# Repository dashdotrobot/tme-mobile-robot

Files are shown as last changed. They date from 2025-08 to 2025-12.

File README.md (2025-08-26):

# tme-mobile-robot
UW Tacoma Mechatronics mobile robotics platform for education

This repository contains 3D models, a parts list, and example code to build a simple two-wheeled robot. The required components are relatively cheap and easily available. A 3D printer and laser cutter are required to manufacture some components.

The robot can be easily extended and customized to accomplish a wide variety of tasks. The base plate has an array of holes which match the diameter and spacing of standard LEGO and LEGO Technic parts.

The robot platform was developed for TME 441 Mechatronics, a required senior-level course in the Mechanical Engineering program at the University of Washington, Tacoma.

## Parts list

### Base kit parts
These components are part of the base kit that every team assembles.

| Part | Qty | Source/Link
| ---- | --- | --- |
| Base plate | 1 | Custom (laser cut)
| Arduino Mega 2560 | 1 | [Amazon](https://www.amazon.com/ELEGOO-Compatible-Arduino-Projects-Compliant/dp/B01H4ZLZLQ)
| Motor bracket | 1 | Custom (3D print)
| Caster bracket - front | 1 | Custom (3D print)
| Caster bracket - rear | 1 | Custom (3D print)
| IR sensor bracket | 1 | Custom (3D print or laser cut)
| Wheel | 2 | Custom (3D print)
| LEGO Tire 81.6 x 15 ([#2902](https://www.bricklink.com/v2/catalog/catalogitem.page?P=2902)) | 2 | Various suppliers
| Gear motor with encoder | 2 | [Amazon](https://www.amazon.com/Encoder-Metal-Gearmotor-Arduino-Printers/dp/B07GNFYGYQ)
| 7.2V Battery pack | 1 | [Amazon](https://amazon.com/dp/B07NWZ4T29)
| Half-sized bread board | 1 | [Adafruit](https://www.adafruit.com/product/64)
| Analog IR sensor | 3 | [SparkFun](https://www.sparkfun.com/sparkfun-line-sensor-breakout-qre1113-analog.html)
| L293D Motor driver | 1 | [Amazon](https://www.amazon.com/Bridgold-16-pin-Stepper-Drivers-Controllers/dp/B07NXTWJV9)
| Ultrasonic sensor HC-SR04 | 1 | [SparkFun](https://www.sparkfun.com/products/15569)
| Plastic ball caster 1/2" | 2 | [Pololu](https://www.pololu.com/product/952)

### Expansion parts
These components are available to each team for use in their custom solution.

| Part | Qty | Source/Link |
| ---- | --- | --- |
| 5V Stepper motor 28BYJ-48 | 2 | [Amazon](https://www.amazon.com/ELEGOO-28BYJ-48-ULN2003-Stepper-Arduino/dp/B01CP18J4A)
| 9g Hobby servo | 2 | [Amazon](https://www.amazon.com/Smraza-Helicopter-Airplane-Control-Arduino/dp/B07L2SF3R4)
| Piezo buzzer | 1 | [Amazon](https://www.amazon.com/BNYZWOT-Electronic-Magnetic-Continuous-Arduino/dp/B07VP6BTMV)

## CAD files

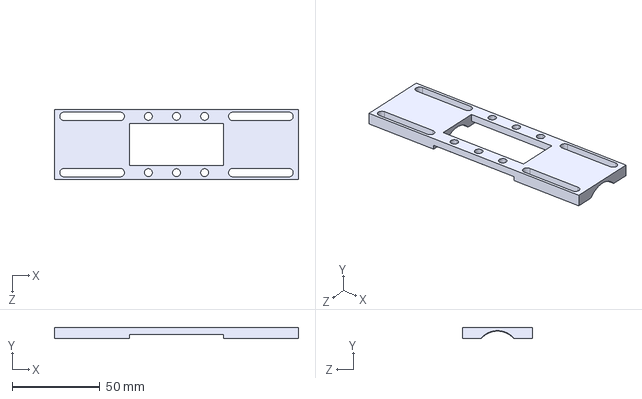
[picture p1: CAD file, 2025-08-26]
manufacturing files/motor_bracket_full.STEP
138.8 x 6.35 x 40.0 mm

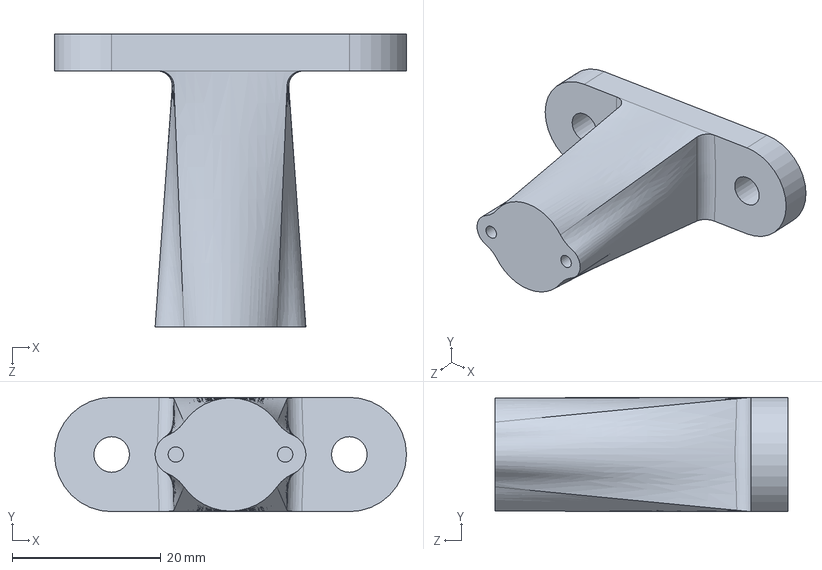
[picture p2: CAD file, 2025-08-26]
3d models/caster_bracket_rear.SLDPRT
47.4 x 15.4 x 39.5 mm

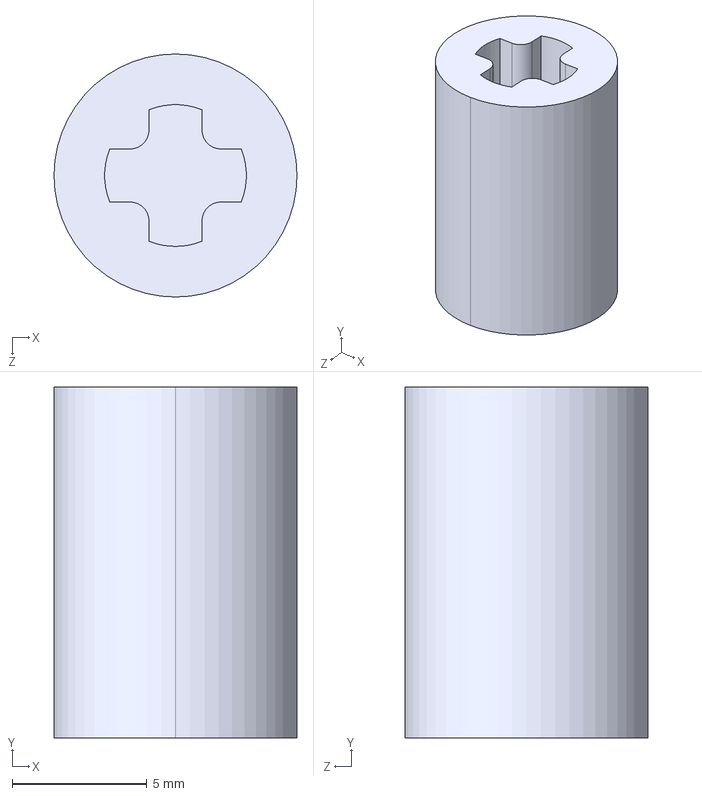
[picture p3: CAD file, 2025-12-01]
manufacturing files/stepper_motor_coupler.STEP
9.00 x 13.0 x 9.00 mm

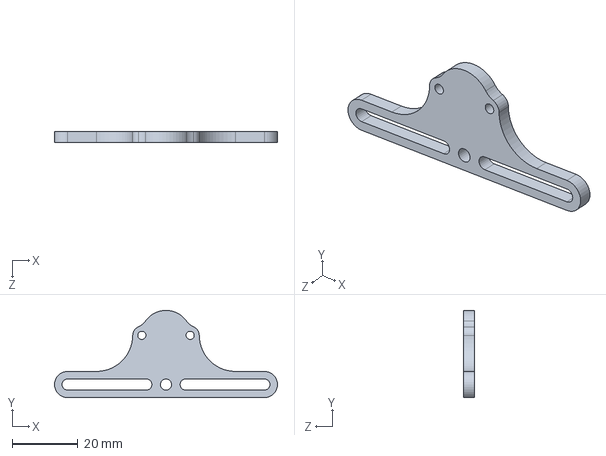
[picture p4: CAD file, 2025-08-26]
3d models/IR_sensor_bracket.SLDPRT
68.0 x 26.6 x 3.50 mm

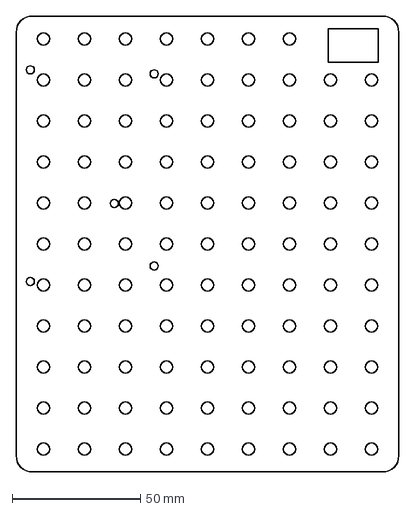
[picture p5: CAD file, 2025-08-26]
manufacturing files/base.DXF
149.2 x 177.8 mm

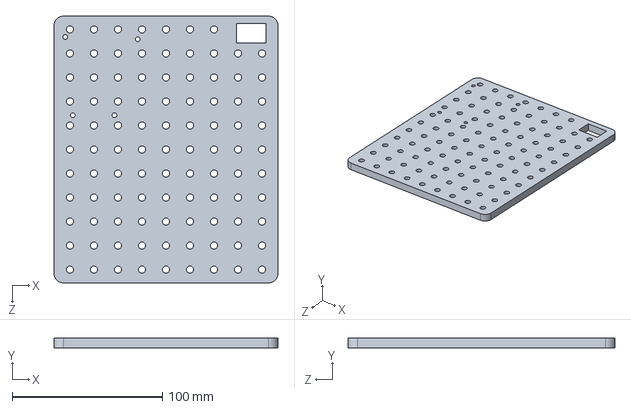
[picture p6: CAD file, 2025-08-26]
3d models/base.SLDPRT
149.2 x 6.35 x 177.8 mm

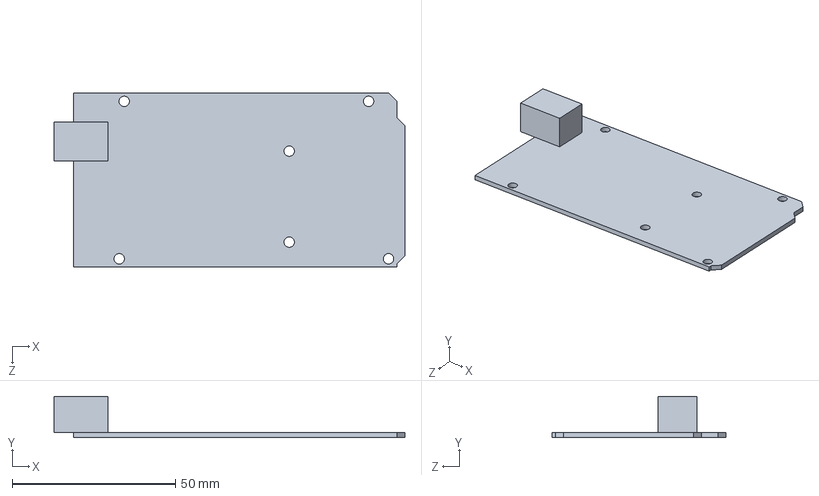
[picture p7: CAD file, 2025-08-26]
3d models/arduino_mega2560.SLDPRT
107.6 x 12.6 x 53.3 mm

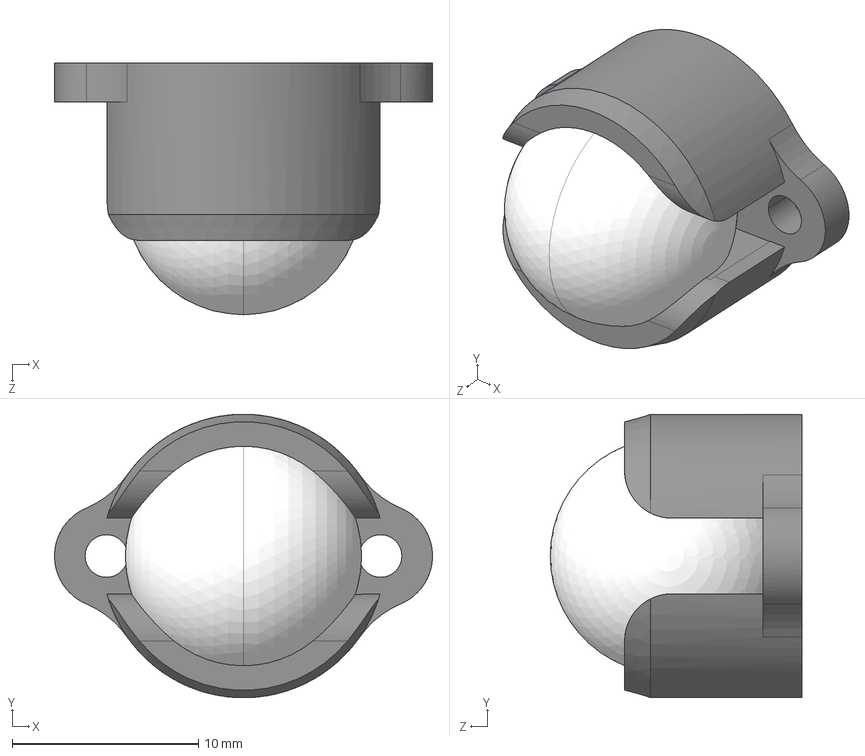
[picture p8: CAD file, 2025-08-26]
3d models/pololu-ball-caster-with-0-500in-ball.step
20.3 x 15.2 x 13.5 mm

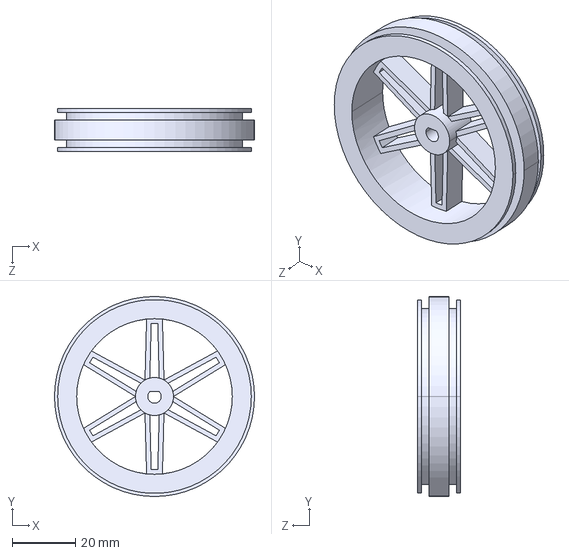
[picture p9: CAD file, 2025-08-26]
manufacturing files/wheel.STEP
63.1 x 63.1 x 13.5 mm

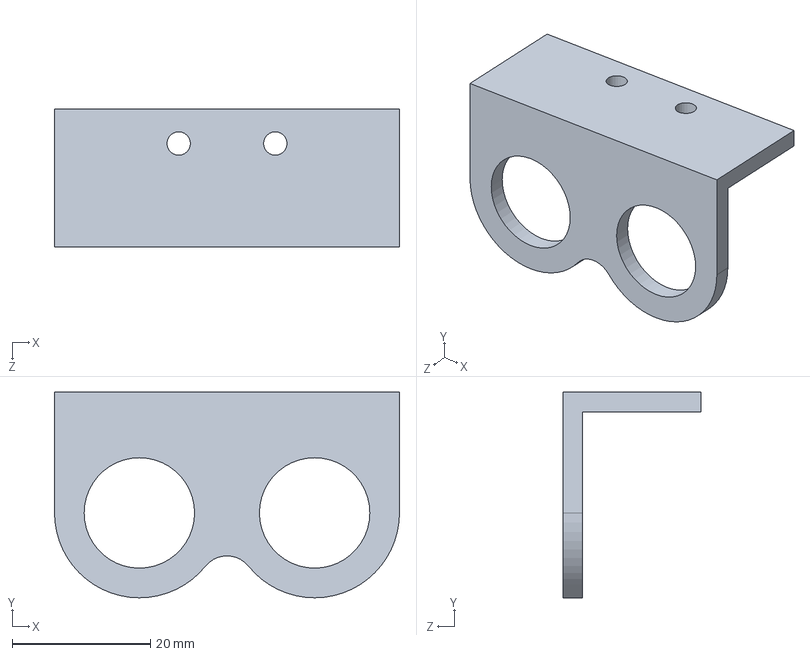
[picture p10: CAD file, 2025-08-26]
3d models/US_sensor_bracket.SLDPRT
50.0 x 29.8 x 20.0 mm

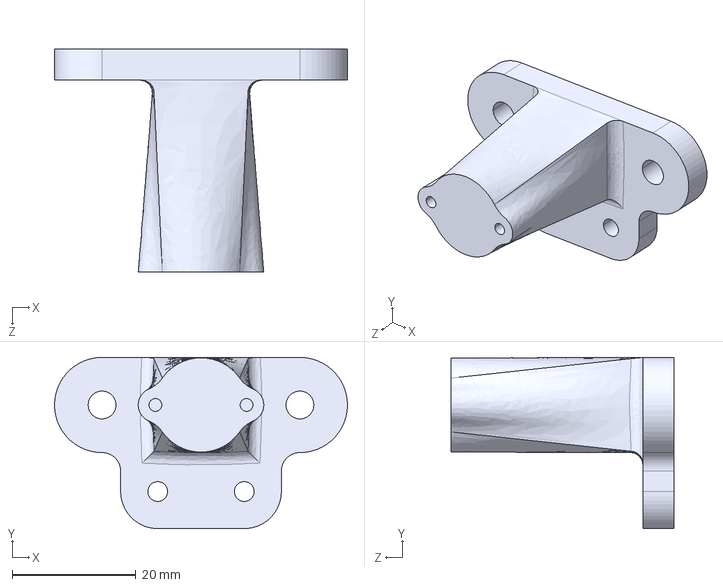
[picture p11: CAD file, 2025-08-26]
manufacturing files/caster_bracket_front.STEP
47.4 x 27.7 x 36.0 mm

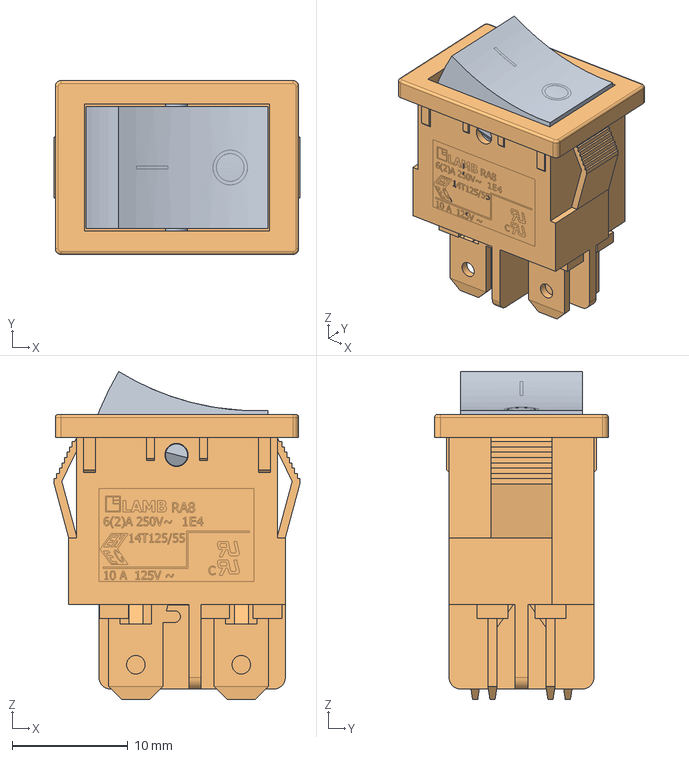
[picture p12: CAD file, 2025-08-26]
3d models/RA8123xxx1.stp
21.2 x 15.0 x 28.3 mm

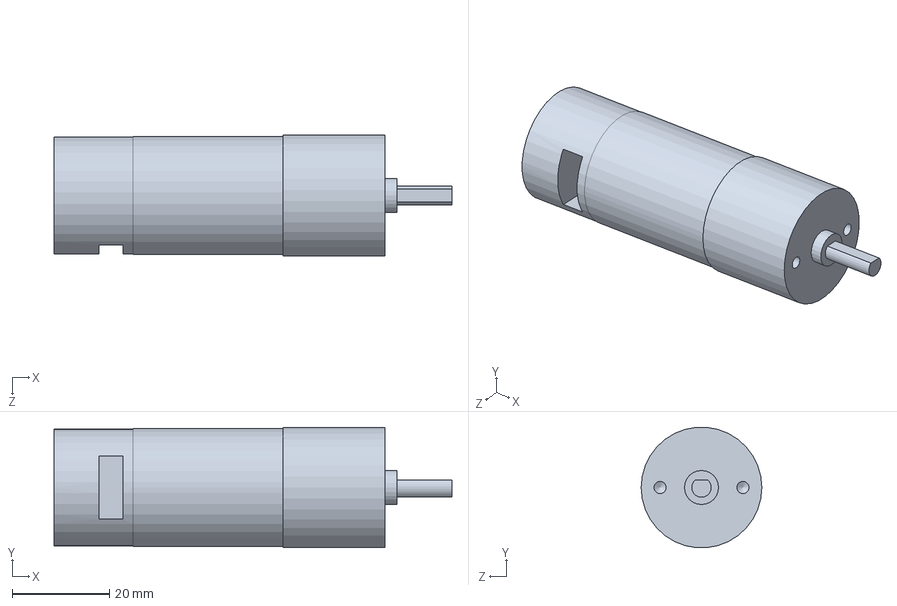
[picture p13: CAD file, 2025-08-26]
3d models/gear_motor.SLDPRT
81.8 x 24.7 x 24.8 mm

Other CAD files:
3d models/motor_bracket_full.SLDPRT
manufacturing files/caster_bracket_rear.STEP
manufacturing files/IR_sensor_bracket.STEP
3d models/wheel.SLDPRT
3d models/caster_bracket_front.SLDPRT
3d models/Mobile Robot.SLDDRW
manufacturing files/stepper_motor_coupler.SLDPRT

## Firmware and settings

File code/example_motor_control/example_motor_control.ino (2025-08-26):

/* UWT-ME Mobile Robot Platform
*  Example: Motor Control
*
*  Control gearmotor speeds with feedback control.
*
*  Set the correct pin numbers in motor_control.h depending on your specific
*  configuration. Change PID_INT and PID_REP_INT to change the feedback loop
*  update interval and the reporting interval (for printing data to the
*  serial monitor), respectively.
*
*  @author Matthew Ford
*/
#include <Encoder.h>
#include "motor_control.h"

void setup() {
  Serial.begin(9600);
  initMotors();  // Configure motor pins
}

void loop() {

  // Drive both motors forwards for 3 sec
  long t_start = millis();
  while ((millis() - t0) <= 3000) {
    updatePID(1500, 1500, true);
  }
  motorHalt(RMOTOR);
  motorHalt(LMOTOR);
  delay(500);

  // Drive both motors backwards for 3 sec
  t_start = millis();
  while ((millis() - t0) <= 3000) {
    updatePID(1500, 1500, true);
  }
  motorHalt(RMOTOR);
  motorHalt(LMOTOR);
  delay(500);

  // Drive motors in opposite directions for 3 sec (each)
  // Spin robot clockwise
  t_start = millis();
  while ((millis() - t0) <= 3000) {
    updatePID(1500, -1500, true);
  }

  // Spin robot counterclockwise
  t_start = millis();
  while ((millis() - t0) <= 3000) {
    updatePID(1500, -1500, true);
  }
  motorHalt(RMOTOR);
  motorHalt(LMOTOR);
  delay(500);

}

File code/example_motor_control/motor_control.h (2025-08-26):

/* Motor Control Library
*  Utilities for configuring and controlling DC motors.
*
*  @author Matthew Ford
*  @version 2024.1
*/

// Define motor control pins
#define RMOTOR 0
#define RMOTOR_DIR_A 6
#define RMOTOR_DIR_B 7
#define RMOTOR_SPD 5

#define LMOTOR 1
#define LMOTOR_DIR_A 10
#define LMOTOR_DIR_B 11
#define LMOTOR_SPD 7

// Define PID options
#define PID_INT 20       // PID update interval [ms]
#define PID_REP_INT 250  // PID report interval [ms]

/* Global variables for PID motor control. You will need to tune these
*  parameters for your own robot. */
const float K_P = 0.1;    // Proportional gain
const float K_I = 0.001;  // Integral gain
const float K_D = 0.1;    // Derivative gain (damping)
const long max_err_i = 255 / K_I;

long last_enc_l = 0;  // Last encoder position [steps]
long last_enc_r = 0;
long last_pid_time = 0;  // Time of last control loop update [microsecs]
long last_pid_rep_time = 0;
long err_int_l = 0;  // Error integrals
long err_int_r = 0;
long last_speed_l = 0;  // Previous measured speed [steps/sec]
long last_speed_r = 0;

// Attach encoders
Encoder enc_r(20, 21);  // Change pin numbers to match your own circuit
Encoder enc_l(18, 19);

// Initialize motors
void initMotors() {
  pinMode(LMOTOR_DIR_A, OUTPUT);
  pinMode(LMOTOR_DIR_B, OUTPUT);
  pinMode(LMOTOR_SPD, OUTPUT);

  pinMode(RMOTOR_DIR_A, OUTPUT);
  pinMode(RMOTOR_DIR_B, OUTPUT);
  pinMode(RMOTOR_SPD, OUTPUT);
}

/* Turn motor on at desired speed
*
*  @param motor Which motor to turn on (LMOTOR or RMOTOR).
*  @param speed Desired speed, -255 to 255. Negative = backwards.
*/
void motorOn(int motor, int speed) {
  if (motor == LMOTOR) {
    digitalWrite(LMOTOR_DIR_A, (speed > 0));
    digitalWrite(LMOTOR_DIR_B, !(speed > 0));
    analogWrite(LMOTOR_SPD, abs(speed));
  } else if (motor == RMOTOR) {
    digitalWrite(RMOTOR_DIR_A, (speed > 0));
    digitalWrite(RMOTOR_DIR_B, !(speed > 0));
    analogWrite(RMOTOR_SPD, abs(speed));
  }
}

/* Stop motor FAST (electronic braking)
*
*  @param motor Which motor to turn on (LMOTOR or RMOTOR).
*/
void motorHalt(int motor) {
  if (motor == LMOTOR) {
    digitalWrite(LMOTOR_DIR_A, LOW);
    digitalWrite(LMOTOR_DIR_B, LOW);
    digitalWrite(LMOTOR_SPD, HIGH);
  } else if (motor == RMOTOR) {
    digitalWrite(RMOTOR_DIR_A, LOW);
    digitalWrite(RMOTOR_DIR_B, LOW);
    digitalWrite(RMOTOR_SPD, HIGH);
  }
}

/* Update motor voltages using feedback control
*
*  This function should be called repeatedly in a fast loop to update
*  the control signals. The PID update interval can be adjusted by
*  changing the constant PID_INT.
*
*  @param speed_l Desired speed of left motor [ticks/second].
*  @param speed_r ...              right motor.
*  @param report Print data to Serial Monitor periodically.
*/
void updatePID(long speed_l, long speed_r, bool report) {

  long curr_time = millis();  // Get current clock time
  long dt = curr_time - last_pid_time;

  if (dt >= PID_INT) {
    // Calculate motor speeds
    long curr_enc_l = enc_l.read();
    long curr_enc_r = enc_r.read();

    long speed_meas_l = (1000 * (curr_enc_l - last_enc_l)) / dt;
    long speed_meas_r = (1000 * (curr_enc_r - last_enc_r)) / dt;

    // Calculate error signals
    long err_l = speed_l - speed_meas_l;
    long err_r = speed_r - speed_meas_r;

    // Update error integrals, with anti-windup correction.
    err_int_l = constrain(err_int_l + err_l * dt, -max_err_i, max_err_i);
    err_int_r = constrain(err_int_r + err_r * dt, -max_err_i, max_err_i);

    // Calculate control signals
    int u_P_l = K_P * err_l;
    int u_P_r = K_P * err_r;
    int u_I_l = K_I * err_int_l;
    int u_I_r = K_I * err_int_r;
    int u_D_l = K_D * ((speed_meas_l - last_speed_l) / dt);
    int u_D_r = K_D * ((speed_meas_r - last_speed_r) / dt);

    int u_l = constrain(int(u_P_l + u_I_l + u_D_l), -255, 255);
    int u_r = constrain(int(u_P_r + u_I_r + u_D_r), -255, 255);

    // Update "memory" variables
    last_enc_l = curr_enc_l;
    last_enc_r = curr_enc_r;
    last_pid_time = curr_time;
    last_speed_l = speed_meas_l;
    last_speed_r = speed_meas_r;

    // Set motor speeds
    motorOn(LMOTOR, u_l);
    motorOn(RMOTOR, u_r);

    // Report values to Serial Monitor
    if (report && (curr_time - last_pid_rep_time) > PID_REP_INT) {
      Serial.print("time:");
      Serial.print(curr_time);
      Serial.print(", v_meas_l:");
      Serial.print(speed_meas_l);
      Serial.print(", v_meas_r:");
      Serial.print(speed_meas_r);
      Serial.print(", voltage_l:");
      Serial.print(u_l);
      Serial.print(", voltage_r:");
      Serial.println(u_r);

      last_pid_rep_time = curr_time;
    }
  }
}

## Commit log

2025-08-26 Upload local resources
    [IR_sensor_bracket.SLDPRT, IR_sensor_bracket.STEP, Mobile Robot.SLDDRW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]
2025-12-01 Upload stepper motor adaptor files
    [stepper_motor_coupler.SLDPRT, stepper_motor_coupler.STEP]
